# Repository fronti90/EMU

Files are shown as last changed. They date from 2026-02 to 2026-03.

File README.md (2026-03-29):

[][cc-by-nc-sa]

# EMU – Expandable Multi-material Unit
### A new take on a MMU by <a href="https://github.com/DW-Tas">DW-Tas</a> and <a href="https://github.com/igiannakas">igiannakas</a><br/>
<a href="https://ko-fi.com/O5O5OCC0K"> Ko-Fi</a>

Join me on Discord (https://discord.gg/hG2NRazKG3)   HappyHare Discord: https://discord.gg/Yt8Fe7FkNc

**Introducing the EMU, the Expandable Multi-material Unit from down under.** The EMU is a modular, flexible, upgradable, reliable and service-friendly MMU designed around the proven filamentalist V3 platform.

The EMU supports any number of lanes and base configurations; whether it is a **single lane setup** to assist filament loading, a **dual lane configuration** for endless spool, or a **multi-lane, multi base unit setup** for multi-material printing. It is also **expandable**, with no re-printing of parts required when upgrading from a 2 lane to a multiple lane setup.

> [!TIP]
> ### Crossbow Filament Cutter And A4T Toolhead
> Make the EMU part of a complete system with the [Crossbow Filament Cutter](https://github.com/DW-Tas/Crossbow-Filament-Cutter) and the [A4T Toolhead](https://github.com/Armchair-Heavy-Industries/A4T).

<p align="center">
  
</p>

### Table of Contents
- [Design Objectives & Key Features](#design-objectives)
- [Render Gallery](#render-gallery)
- [Prints Gallery](#prints-gallery)
- [Documentation](/docs)
  - [BOM, Printing, Assembly and Wiring instructions](/docs/assembly_wiring)
  - [Software Setup and Calibration](/docs/software_setup)
  - [Slicer setup and optimisation for multi color prints](/docs/software_setup/05-slicer-setup.md)
- [License](#this-work-is-licensed-under-a)

### Highlights
- **Modular & Expandable** design, able to add lanes anytime and in any configuration. No reprints when upgrading from a 2 lane setup.
- **One screw or tool-free** access and servicing, even mid-print.
- **Sealed dry boxes** able to maintain humidity in the 15% range (with silica gel) or 5–8% range (with molecular sieves) for weeks.  
- **Humidity sensors** per lane for filament environmental monitoring.
- **Reliable endless spool** with no chance of the rewound filament interfering with neighbouring rolls.
- **Off-the-shelf electronics** (EBB42 with EBB36 also fully compatible).  
- **Per-lane controls** - eject button + LEDs.

<p align="center">
  
  
</p>

## Design Objectives

### Modularity & Upgradeability  
Each lane is fully self-contained, so you can choose **exactly how many lanes you need and group them as you like**. You can also **mix and match** lanes across multiple base units, or use a stand-alone single lane for extruder loading and print assistance. 

Expanding later is also straightforward. Just print lane expanders for the base and add another dry box assembly. There is no need to reprint or replace existing parts when upgrading from a 2 lane base. 

### Ease of Servicing 
All electrical and mechanical components are either **one screw or completely tool-free and immediately accessible**, making live troubleshooting possible even during a print. 

Access to the electronics is easy - just lift the dry box off its base for full access. The stepper tensioning screw is accessible without any dissassembly allowing on the fly tuning of filament grip. Finally, removing the filamentalist, stepper and stepper assembly is possible via one screw.

### Sealed Dry Boxes  
Each spool sits in its own purpose built, **fully sealed dry box with an integrated desiccant holder**. The boxes use foam cord in areas of potential air ingress to create a tight seal, with the clear 1.5mm PETG/PC panel also offering visibility inside the dry box.

The dry boxes can maintain humidity in the 15% range (with silica gel) or 5–8% range (with molecular sieves) for weeks. Finally, as each dry box is self contained, opening one to reload filament, doesn’t disturb its neighbours, extending the effective desiccant life.

<p align="center">
  
</p>

### Integrated Humidity Sensors 
Each lane monitors its own environment, letting you know when it’s **time to refresh the desiccant**. The humidity sensors are integrated into Mainsail (and optionally in Home Assistant for historical data tracking via the mainsail HA integration).

### Endless Spool Reliability
Dual pre-stepper sensors ensure **consistent run-out detection** and reliable re-wind, as the filament is always gripped by the stepper hobbed gear assembly. 

In addition, the isolated boxes ensure that any left over, rewound, filament cannot interfere with neighbouring lanes, **preventing a jam**.

### Built on the Filamentalist
The lane assembly is based on the proven **[filamentalist V3 design with 688 bearings](https://github.com/Enraged-Rabbit-Community/ERCF_v2/tree/master/Recommended_Options/Filamentalist_Rewinder/Filamentalist_FV3_Rewinder)** with wide spool size compatibility. Built on the 74mm filamentalist stock setup, the unit fits even the slighlty wider KVP filament spools.

<p align="center">
  
  
</p>

### Integrated Filament Driving Stepper 
Each lane has its own driving stepper inside the dry box, resulting in a compact, **fully self-contained mechanical design**. In case of mechanical issue, you can swap out filamentalist assemblies with 3 screws, unplugging 2 JST plugs and unplugging the bowden tube. 

In addition, you can **swap out complete dry boxes** by unplugging two JST plugs and the bowden tube. This is helpful if you want to maintain a particularly moisture sensitive filament undisturbed when swapping it out from the EMU.

### Simple Electronics
The recommended BOM uses **readily available EBB42 boards** (with EBB36 fully compatible). MMB v2 boards can also be reused, though without humidity sensing due to I²C limitations and a slightly more intricate wiring.

In addition, **each lane has its own ventilation fan**, ensuring the stepper drivers do not overheat, even when the unit is placed on top of a hot printer. With the EBB42 and EBB36, the ventilation fans can also be speed controlled to minimize noise.

### Easy mounting
The EMU base assembly can be securely **mounted on extrusions** or using **rubber feet** directly on the printer or besides it. In either case the **electronics remain accessible** without needing to remove the unit from its mounts.

### Per-lane Controls  
Each lane includes its own eject button, status LED, and a filament colour LED that illuminates the dry box. 

## Render Gallery
<p align="center">
  
  
</p>
<p align="center">
  
  
</p>
<br/>

## Prints Gallery
<p align="center">
  1 (4)
  1 (5)
  1 (2)
  1 (3)
</p>

## Mods to main
The following mods from the community have been adopted into the main EMU release
 - Rim roller with square nuts: [martijnvanduijneveldt](https://github.com/martijnvanduijneveldt)
 - EMU Wiring Hatch Board: [kashine6](https://github.com/kashine6)

## This work is licensed under a
[Creative Commons Attribution-NonCommercial-ShareAlike 4.0 International License][cc-by-nc-sa].

[][cc-by-nc-sa]

[cc-by-nc-sa]: http://creativecommons.org/licenses/by-nc-sa/4.0/
[cc-by-nc-sa-image]: https://licensebuttons.net/l/by-nc-sa/4.0/88x31.png
[cc-by-nc-sa-shield]: https://img.shields.io/badge/License-CC%20BY--NC--SA%204.0-lightgrey.svg

## License clarification regarding non-commercial use:
The non-commercial aspect of this license is for cases where EMU is the product, not the use of EMU to create products.<br/>
I.e. If you wish to sell EMU as a product, you would need to seek a commercial license before doing so. </br>
It is NOT intended to prevent the use of EMU with a printer that you use to provide commercial services. If you want to run EMU in your print farm, go right ahead.

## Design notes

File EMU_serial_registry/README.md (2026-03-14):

# EMU – Expandable Multi-material Unit - Official Serial Registry

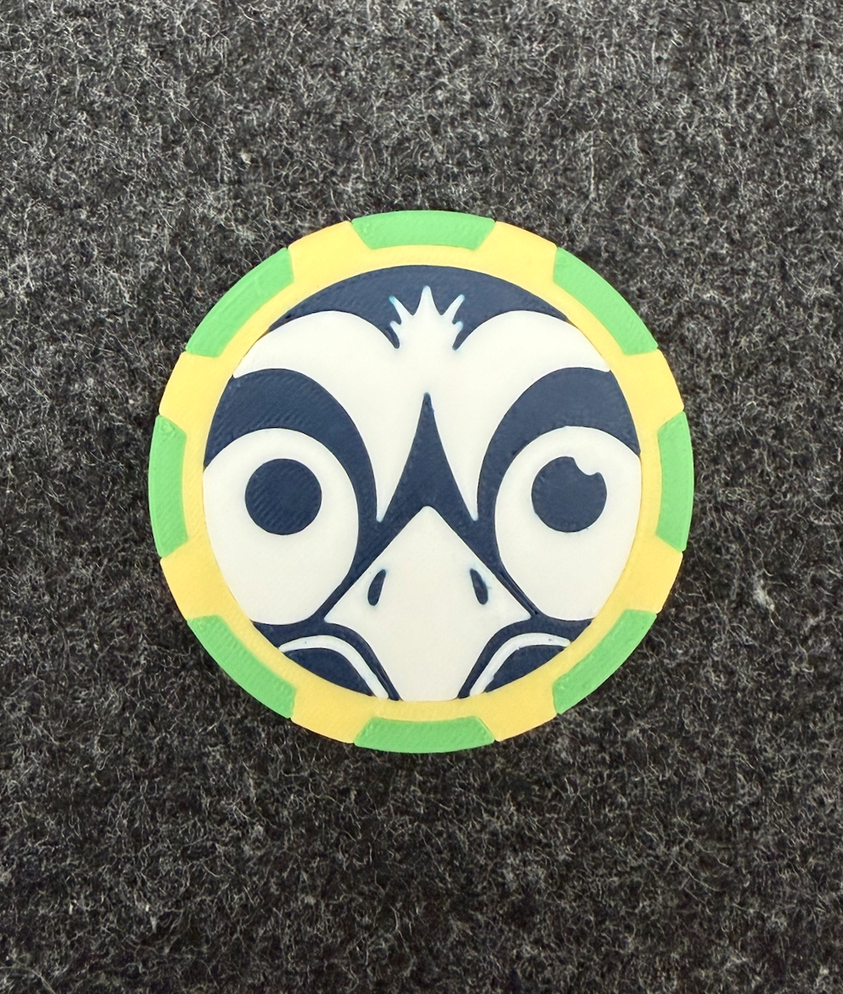
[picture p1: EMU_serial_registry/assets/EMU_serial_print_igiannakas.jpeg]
EMU Serial Print by igiannakas


**Serial #0000:** DW Tas</br>
**Serial #0001:** igiannakas</br>
**Serial #0002:** Martijn</br>
**Serial #0003:** burkfers</br>
**Serial #0004:** WilLawUK</br>
**Serial #0005:** jacksky6</br>
**Serial #0006:** Heiliger-Gral</br>
**Serial #0007:** drachenkaetzchen</br>
**Serial #0008:** fronti</br>
**Serial #0009:** pajtaz</br>
**Serial #0010:** WoodWorker</br>
**Serial #0011:** Dragi2k</br>
**Serial #0012:** TheMeanCanEHdian</br>
**Serial #0013:** Bender</br>
**Serial #0014:** Pie36</br>
**Serial #0015:** ammaze</br>
**Serial #0016:** Doak</br>
**Serial #0017:** dw.tas</br>
</br>

### How to register:
Submit your build at [dwtas.net/EMUSerial](https://dwtas.net/EMUSerial). Sign in with Discord, upload a photo of your completed EMU Maker chip and unit, and a maintainer will review your submission.

Print [at least a two color version of the EMU Maker chip](https://github.com/DW-Tas/EMU/tree/main/EMU_serial_registry/serial_print_file). If your EMU lane can reach 4+ colors, try to use them all!

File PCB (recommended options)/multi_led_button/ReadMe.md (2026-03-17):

## EMU LED PCB

The **EMU LED PCB** is a dedicated PCB designed for the EMU to enable dynamic lighting effects on the eject button assembly. It also simplifies wiring and reduces the need for soldering.

LED PCB

## BOM variations vs. baseline EMU BOM
Do not purchase the below from the base BOM:
1. 1 less neopixel
2. 1 less D2F-L switch
3. 4 less 6x3mm magnets

Add the below to the base BOM, depending on your LED PCB source:
1. 1x JST-XH 5 pin PCB header

## Manual
Assembly and wiring instructions are outlined [in the manual](https://github.com/DW-Tas/EMU/blob/main/PCB%20(recommended%20options)/multi_led_button/EMU%20LED%20Button%20PCB%20Assembly%20Manual.pdf).

## Sourcing
The hatch board PCBs can be sourced from the below location:
1. [Aliexpress](https://www.aliexpress.com/item/1005011529532141.html) in sets of 5

Alternatively use the supplied gerber, BOM and pick and place files to order from your favourite PCB manufacturer.

## Lighting effects
The multiple LEDs incorporated in the eject button allow you to create loading/unloading animations like the below. Also the integrated SMD switch provides a more tactile feel vs. the D2F switch and magnet assembly. 

The lighting effects are enabled automatically by happy hare. No separate configuration is required.

https://github.com/user-attachments/assets/2f268710-e0a5-41e1-b007-02235ff379cc

## This work is licensed under a
[Creative Commons Attribution-NonCommercial-ShareAlike 4.0 International License][cc-by-nc-sa].

[][cc-by-nc-sa]

[cc-by-nc-sa]: http://creativecommons.org/licenses/by-nc-sa/4.0/
[cc-by-nc-sa-image]: https://licensebuttons.net/l/by-nc-sa/4.0/88x31.png
[cc-by-nc-sa-shield]: https://img.shields.io/badge/License-CC%20BY--NC--SA%204.0-lightgrey.svg

## License clarification regarding non-commercial use:
The non-commercial aspect of this license is for cases where EMU is the product, not the use of EMU to create products.<br/>
I.e. If you wish to sell EMU as a product, you would need to seek a commercial license before doing so. </br>
It is NOT intended to prevent the use of EMU with a printer that you use to provide commercial services. If you want to run EMU in your print farm, go right ahead.

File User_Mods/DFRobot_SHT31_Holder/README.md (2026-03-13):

# DFRobot SHT31 Temperature & Humidity Sensor Holder

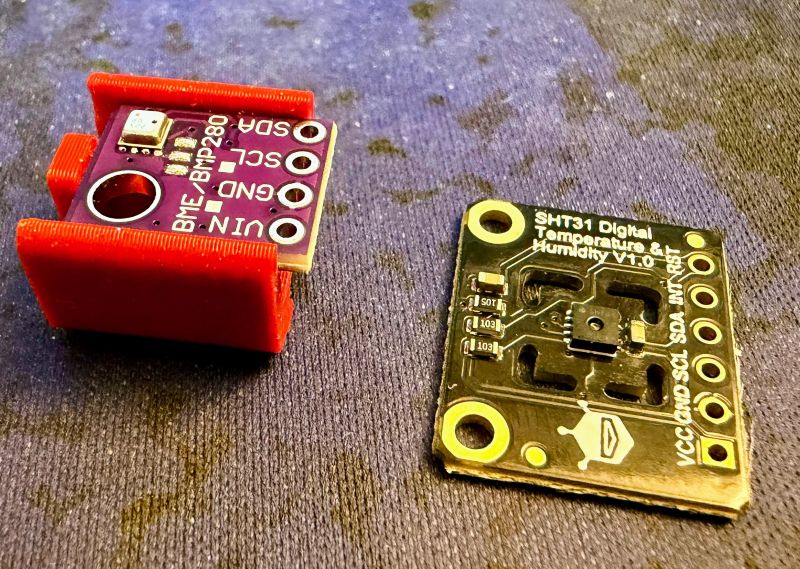
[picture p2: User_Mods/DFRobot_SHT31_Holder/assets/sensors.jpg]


## Overview
High(er) accuracy temperature & humidity sensor for use in the box instead of the standard BME280.

- Pros
    - ±2%RH at 0%RH to 100%RH (at 25°C）humidity accuracy Vs. ±3%RH 20%RH to 80%RH
    - -40°C to 125°C temperature detection range Vs. -40°C to 85°C range (although if its that hot, you've got bigger problems!)
    - Legit Fermion sensor Vs. potential BME280 clones

- Cons
    - Bigger footprint
    - More expensive (~£7 Vs. £4 per sensor)

## BOM
- DFRobot part no: SEN0331

## Where to get them?

Stick to suppliers with a known supply chain.

#### Worldwide
- [Mouser](https://www.mouser.co.uk/ProductDetail/DFRobot/SEN0331)
- [Digikey](https://www.digikey.co.uk/en/products/detail/dfrobot/SEN0331/12324931)

#### UK
- [ThePiHut](https://thepihut.com/products/fermion-sht31-digital-temperature-humidity-sensor?variant=42046092607683)
- [Farnell](https://uk.farnell.com/dfrobot/sen0331/temp-humidity-sensor-breakout/dp/4308263)

## Print settings
Standard EMU settings (999 walls) with shrinkage factor for your chosen filament.

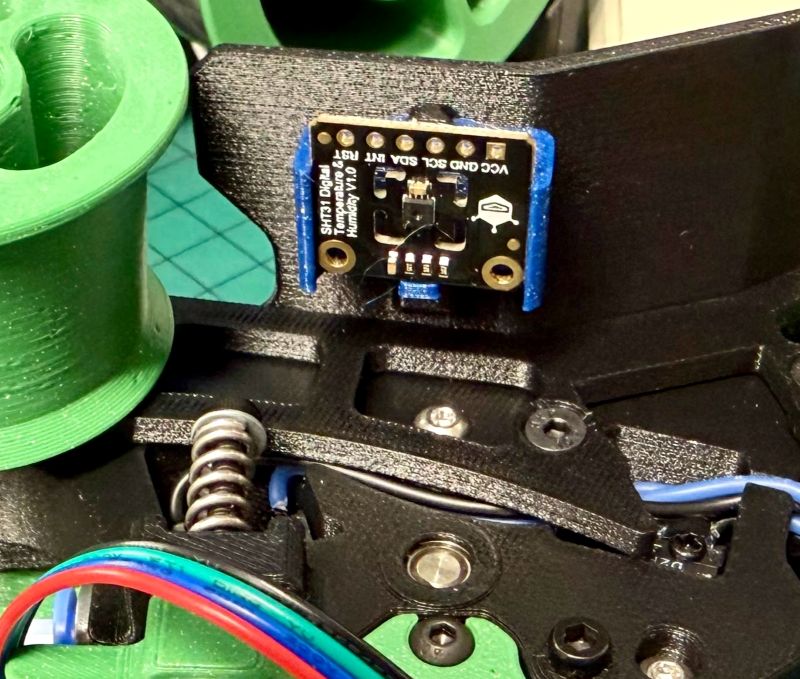
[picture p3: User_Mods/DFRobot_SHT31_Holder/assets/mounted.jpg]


## Code

By default the SHT3X klipper module expects the sensor on 68 (0x44), however the DFRobot sensors can be found at 69 (0x45) unless ADR is connected to connected to GND.

#### Example config for Lane_0 found in emu_macros.cfg

    [temperature_sensor Lane_0]
    sensor_type: SHT3X
    i2c_address: 69
    i2c_mcu: mmu0
    i2c_software_scl_pin: mmu0:PB3
    i2c_software_sda_pin: mmu0:PB4

#### How it should look when working (4 lane example)

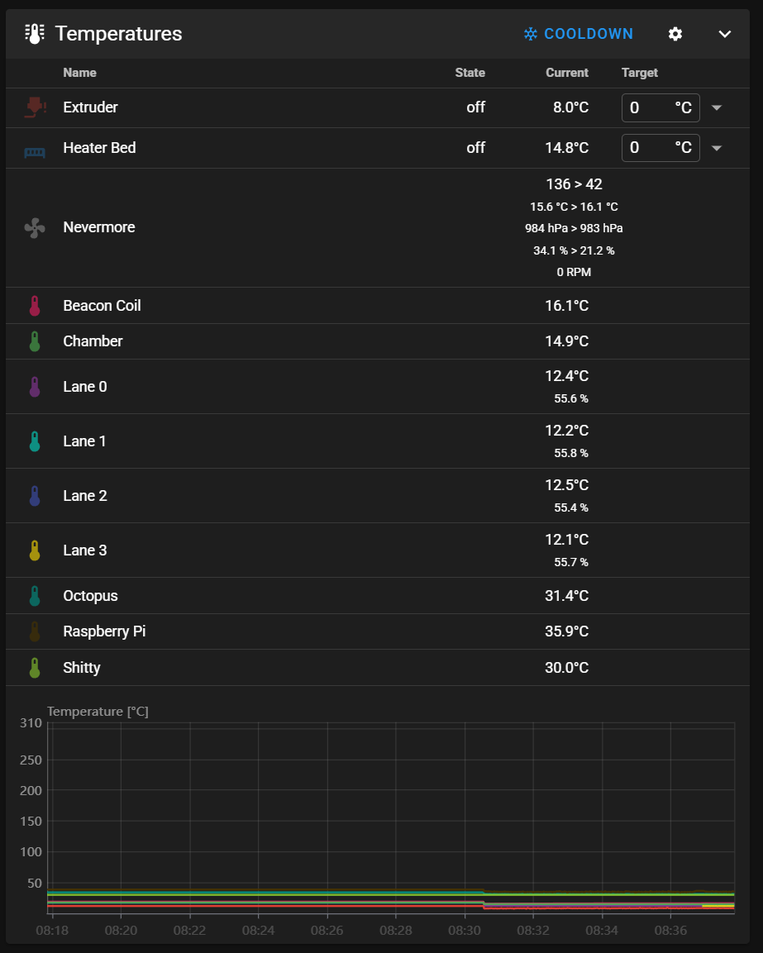
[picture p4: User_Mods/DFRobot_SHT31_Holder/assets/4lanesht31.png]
Working example


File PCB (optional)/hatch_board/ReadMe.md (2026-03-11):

## EMU Wiring Hatch Board

The **EMU Wiring Hatch Board** is a dedicated PCB designed for EMU to make wiring and assembly easier and more convenient. It replaces the printed hatch ([Box_wiring_hatch](https://github.com/DW-Tas/EMU/blob/main/STL/Box/%5Ba%5D_Box_wiring_hatch.stl)), eliminates the need to solder the Filamentalist assembly wires to the JST connectors, and removes the need to use silicone to seal gaps around the JST connector.

The EMU Wiring Hatch Board was designed and developed by <a href="https://github.com/kashine6">kashine6</a>.

## Key Features

1. **Eliminates the need to solder wires directly to JST connectors**
   - Simplifies assembly
   - Reduces soldering complexity
   - Improves maintainability, as the Filamentalist assembly can be easily unplugged from inside the base unit

2. **Simplified pre-stepper sensor connections**
   - The two pre-stepper switches no longer need to be soldered in parallel. Instead, solder the sensor and ground wires to each switch individually, then plug them into the board separately.

3. **Easier box sealing**
   - Removes the need to use silicone to seal the JST connector on the hatch cover.

4. **Wire labeling**
   - Wire labels on the PCB silkscreen reduce the chance of wiring errors during assembly.



## BOM variations vs. baseline EMU BOM
Due to the PCB being thinner than the printed box wiring hatch, **the 2x M3x8mm FHCS screws are now replaced by 2x M3x6 BHCS/SHCS screws**.

If buying pre-assembled, the corresponding straight through hole PCB header JST connectors in the BOM are no longer needed (1x JST XH 8 pin plug and 1x JST XH 4 pin plug).

If making your own, or buying bare PCBs and soldering the JST headers yourself, you'll need the below JST PCB headers:
- 3x JST XH Series Straight Through Hole PCB Header, 4 Contact
- 3x JST XH Series Straight Through Hole PCB Header, 2 Contact
- 1x JST XH Series Straight Through Hole PCB Header, 8 Contact **(part of the EMU BOM)**
- 1x JST XH Series Straight Through Hole PCB Header, 4 Contact **(part of the EMU BOM)**

## Assembly
The soldering order for the JST XH headers is important. **First, solder the 8-pin and 4-pin headers on the “outer” side (the side with the EMU logo).** Then insert and solder the headers on the inner side of the PCB.

Use a hot soldering iron (320-340C) with a medium/thin tip.

## Sourcing
The hatch board PCBs can be sourced from the below two locations:
1. [Aliexpress](https://www.aliexpress.com/item/1005011529532141.html) in sets of 5
2. [JB3D](https://jb3d.uk/product/emu-hatch-pcb/) in individual sets.

## This work is licensed under a
[Creative Commons Attribution-NonCommercial-ShareAlike 4.0 International License][cc-by-nc-sa].

[][cc-by-nc-sa]

[cc-by-nc-sa]: http://creativecommons.org/licenses/by-nc-sa/4.0/
[cc-by-nc-sa-image]: https://licensebuttons.net/l/by-nc-sa/4.0/88x31.png
[cc-by-nc-sa-shield]: https://img.shields.io/badge/License-CC%20BY--NC--SA%204.0-lightgrey.svg

## License clarification regarding non-commercial use:
The non-commercial aspect of this license is for cases where EMU is the product, not the use of EMU to create products.<br/>
I.e. If you wish to sell EMU as a product, you would need to seek a commercial license before doing so. </br>
It is NOT intended to prevent the use of EMU with a printer that you use to provide commercial services. If you want to run EMU in your print farm, go right ahead.

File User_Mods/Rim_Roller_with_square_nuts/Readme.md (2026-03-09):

# Rim roller with square nuts

A remix to use square nuts to secure the rim rollers instead of screwing directly into the plastic.

> The 1 hole version has been adopted and now resides in `STL/Filamentalist` folder.

| 1 Hole | 3 Holes |
|---|---|
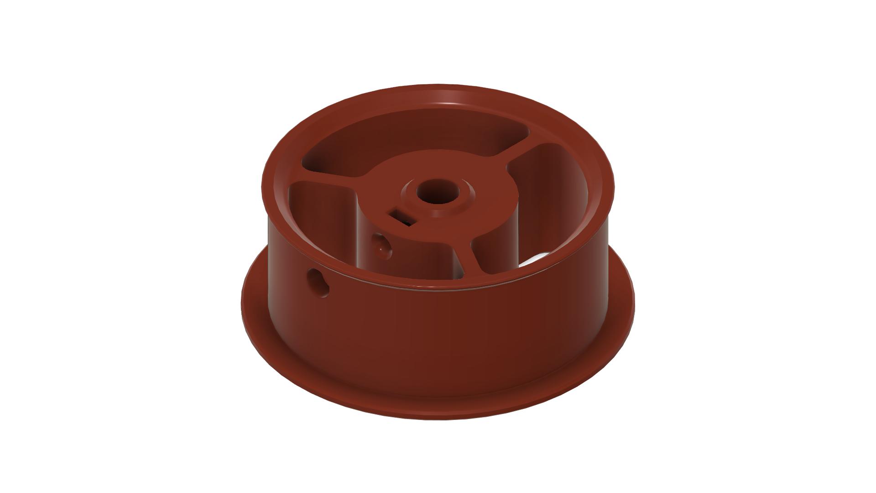
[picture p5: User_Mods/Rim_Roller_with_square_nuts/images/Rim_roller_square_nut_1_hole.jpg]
1 Hole variation
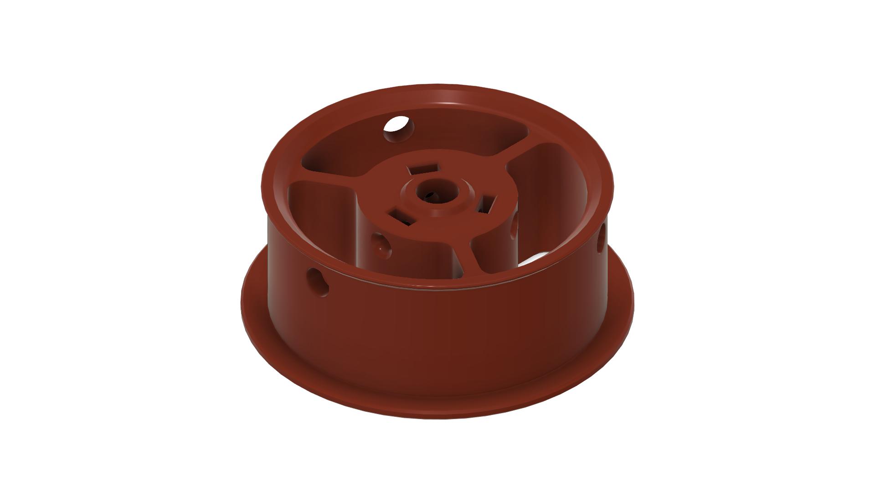
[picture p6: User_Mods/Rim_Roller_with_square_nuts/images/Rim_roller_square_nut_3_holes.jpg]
3 Holes variation
|  |  |

## Credits
- Original mod by [martijnvanduijneveldt](https://github.com/martijnvanduijneveldt)
- Improved by [DW Tas](https://github.com/DW-Tas)

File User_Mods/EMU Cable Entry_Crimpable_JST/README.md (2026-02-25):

# EMU Cable Entry with Cimpable JST sockets

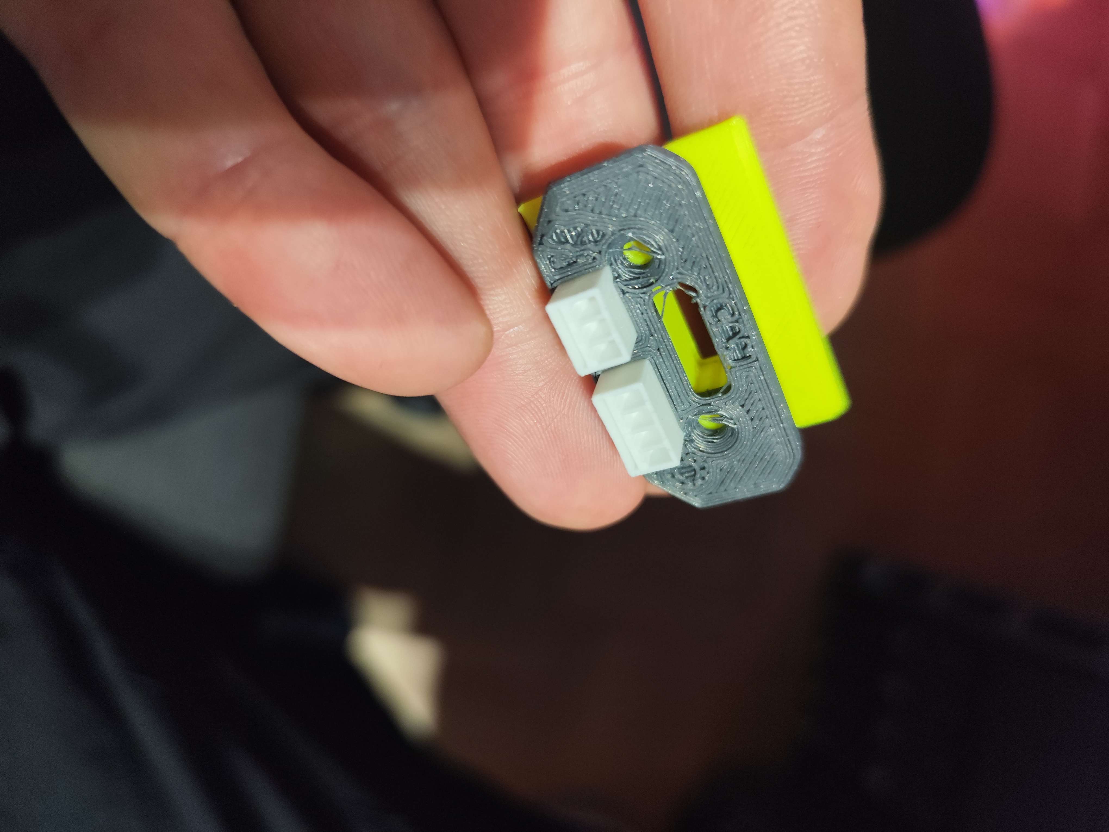
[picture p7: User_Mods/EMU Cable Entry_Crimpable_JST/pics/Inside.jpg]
Inside


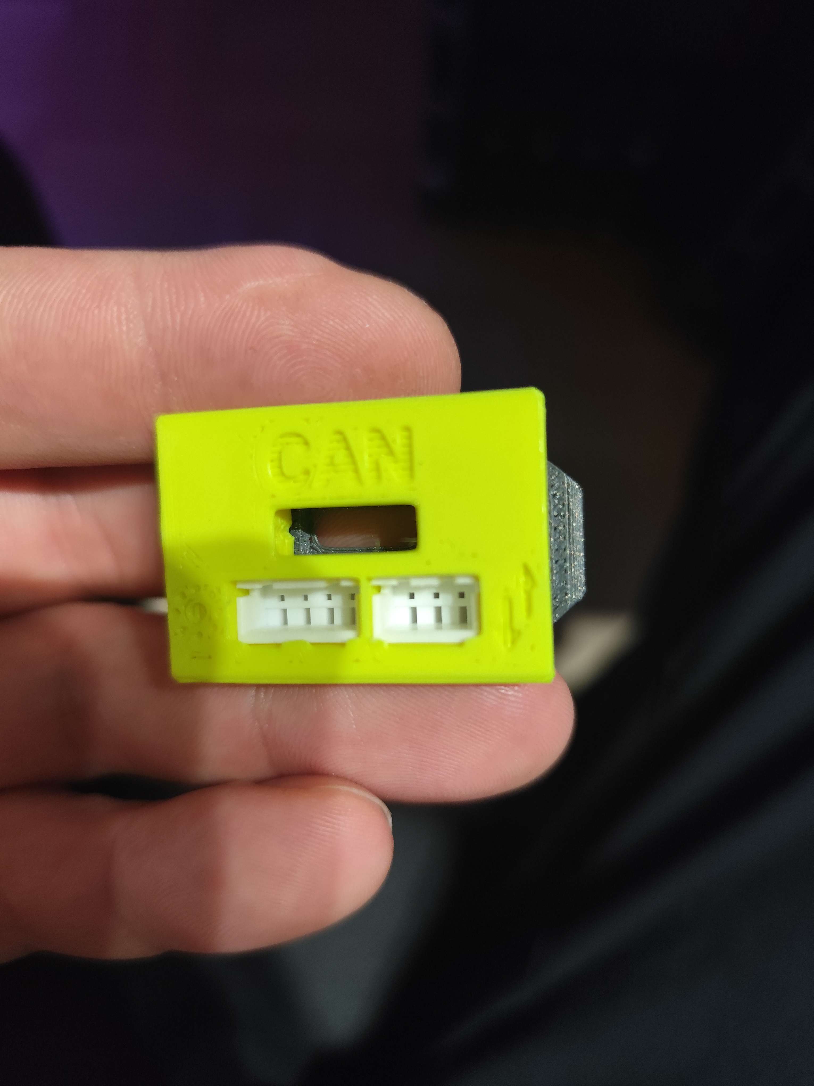
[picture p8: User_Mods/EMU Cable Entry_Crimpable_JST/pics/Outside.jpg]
Outside


for the 3 and 4 pin use these : 

https://de.aliexpress.com/item/1005008063018644.html

https://de.aliexpress.com/item/1005007287524489.html

or

https://de.aliexpress.com/item/1005009495585754.html

you need :

1x 3 pin
1x 4 pin 
per In/outled

the can bus is the origin from the BOM

by Dragi2k

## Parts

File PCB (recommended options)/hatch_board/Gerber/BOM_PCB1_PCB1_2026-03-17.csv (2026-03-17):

No. | Quantity | Comment | Designator | Footprint | Value | Manufacturer Part | Manufacturer | Supplier Part | Supplier | LCSC Part Name | Primary Category | Secondary Category
1 | 1 | PRE*2 | CN4 | CONN-TH_2P-P2.50_HX25003-2A |  | PRE*2 | HX25003-2A | C442299 | LCSC | 1x2P 间距:2.5mm 直插 系列:XH
2 | 1 | 8p | CN7 | CONN-TH_8P-P2.50-XH2.54-8P |  | 8p | Megastar(兆星) | C7429638 | LCSC | 1x8P 间距:2.5mm 直插 系列:XH
3 | 1 | SDA SCL GND 5V | I2C | CONN-TH_4P-P2.50_4PIN |  | SDA SCL GND 5V | Megastar(兆星) | C7429634 | LCSC | 1x4P 间距:2.5mm 直插 系列:XH
4 | 1 | OUT IN GND 5V | LED | CONN-TH_4P-P2.50_4PIN |  | OUT IN GND 5V | Megastar(兆星) | C7429634 | LCSC | 1x4P 间距:2.5mm 直插 系列:XH
5 | 1 | STEP | MOTOR | CONN-TH_4P-P2.50_4PIN |  | STEP | Megastar(兆星) | C7429634 | LCSC | 1x4P 间距:2.5mm 直插 系列:XH
6 | 1 | B2 B1 A1 A2 | MOTOR2 | CONN-TH_4P-P2.50_4PIN |  | B2 B1 A1 A2 | Megastar(兆星) | C7429634 | LCSC | 1x4P 间距:2.5mm 直插 系列:XH
7 | 1 | GND S | POST | CONN-TH_2P-P2.50_HX25003-2A |  | GND S | HX(Zhejiang Yueqing Hongxing Elec) | C442299 | LCSC | 1x2P 间距:2.5mm 直插 系列:XH
8 | 1 | GND S GND S | PRE*2 | CONN-TH_2P-P2.50_HX25003-2A |  | GND S GND S | HX(Zhejiang Yueqing Hongxing Elec) | C442299 | LCSC | 1x2P 间距:2.5mm 直插 系列:XH

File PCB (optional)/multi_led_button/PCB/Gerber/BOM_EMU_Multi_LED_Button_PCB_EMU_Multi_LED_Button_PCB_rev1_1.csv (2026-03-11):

No. | Quantity | Comment | Designator | Footprint | Value | Manufacturer Part | Manufacturer | Supplier Part | Supplier | LCSC Part Name | Primary Category | Secondary Category
1 | 4 | 100nF | C1,C2,C3,C4 | C0603 | 100nF | CC0603KRX7R9BB104 | YAGEO(国巨) | C14663 | LCSC | 100nF ±10% 50V | Capacitors | Multilayer Ceramic Capacitors MLCC - SMD/SMT
2 | 1 | XH2.54-5P | CN1 | CONN-TH_5P-P2.54_C9900008095 |  | XH2.54-5P |  | C9900017328 | LCSC | XH2.54-5P
3 | 4 | SK6812MINIRGBW-NW-P6 | LED1,LED2,LED3,LED4 | LED-ARRAY-SMD_6P-L3.7-W3.5-TL-RD-1 |  | SK6812MINIRGBW-NW-P6 | 欧思科光电 | C7423107 | LCSC | SK6812MINIRGBW-NW-P6 | Optoelectronics | RGB LEDs(Built-in IC)
4 | 1 | GT-TC029D-H020-L1N | SW1 | SW-SMD_L3.9-W2.9-LS4.8 |  | GT-TC029D-H020-L1N | G-Switch(品赞) | C2837082 | LCSC | 3.9*2.9*2mm 立贴 轻触开关 | Switches | Tactile Switches

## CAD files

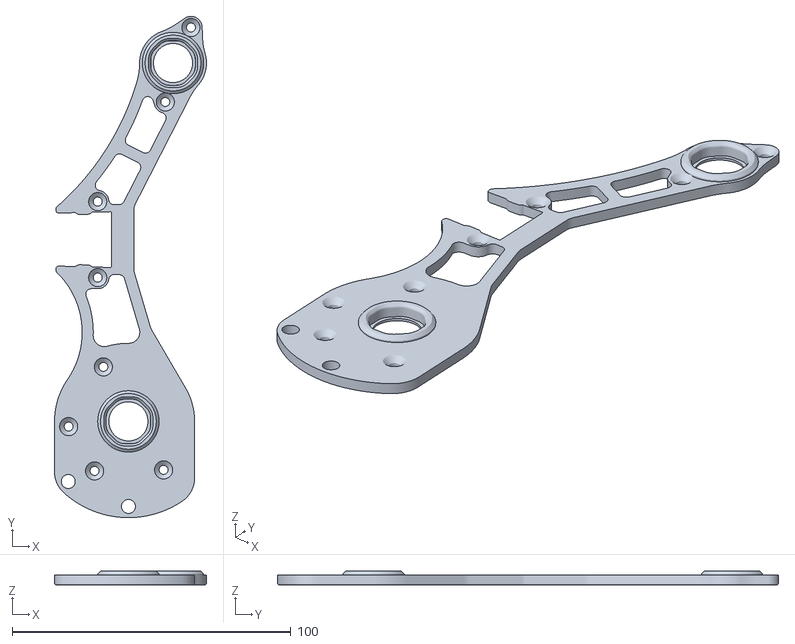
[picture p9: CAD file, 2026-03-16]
Beta parts (parts currently in testing)/Filamentalist_frame_polyhole_bearings/Chassis_L_688_Bearing_8_faces_0.05_inset.stl
54.5 x 179.7 x 5.00

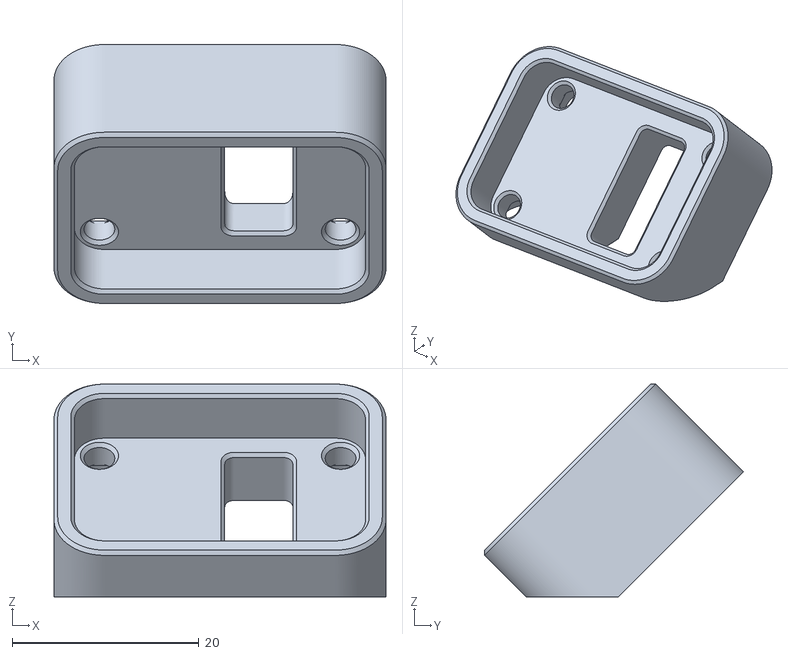
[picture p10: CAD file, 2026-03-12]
PCB (recommended options)/multi_led_button/STL/Button_Rear.stl
35.6 x 27.8 x 22.8

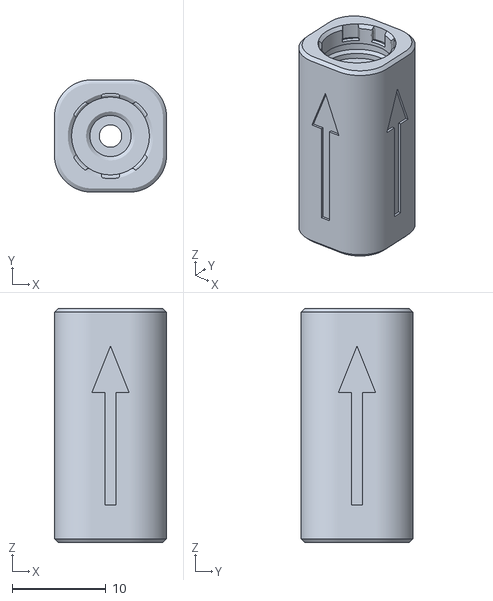
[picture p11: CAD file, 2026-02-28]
STL/Combiner/Combiner_1-1.stl
12.0 x 12.0 x 25.0

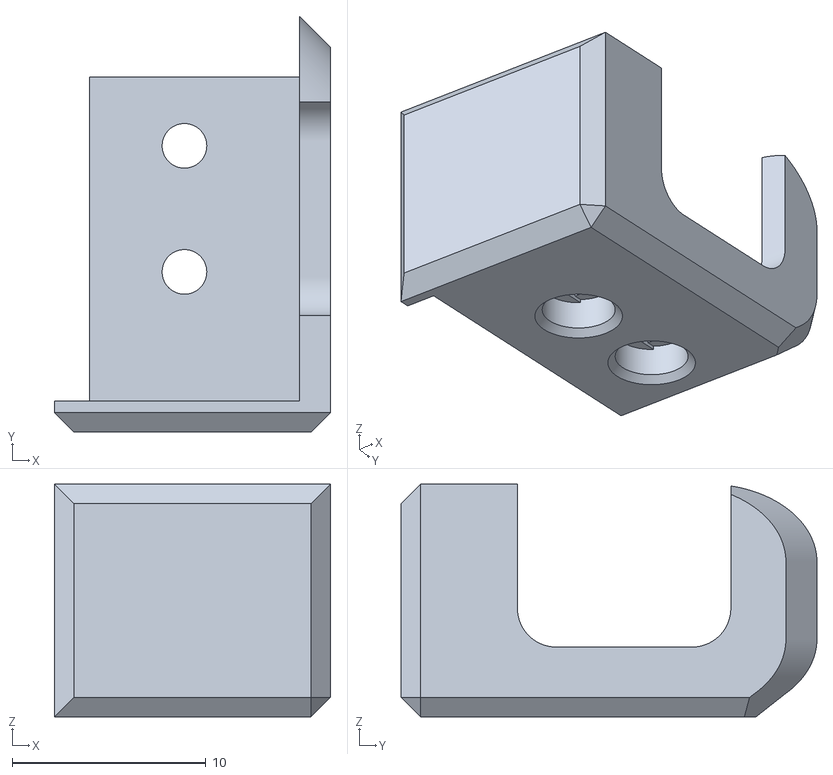
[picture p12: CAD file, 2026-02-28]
STL/Combiner/Optional/Combiners_with_sensor/[a]Combiner_sensor_cap.stl
14.2 x 21.4 x 12.0

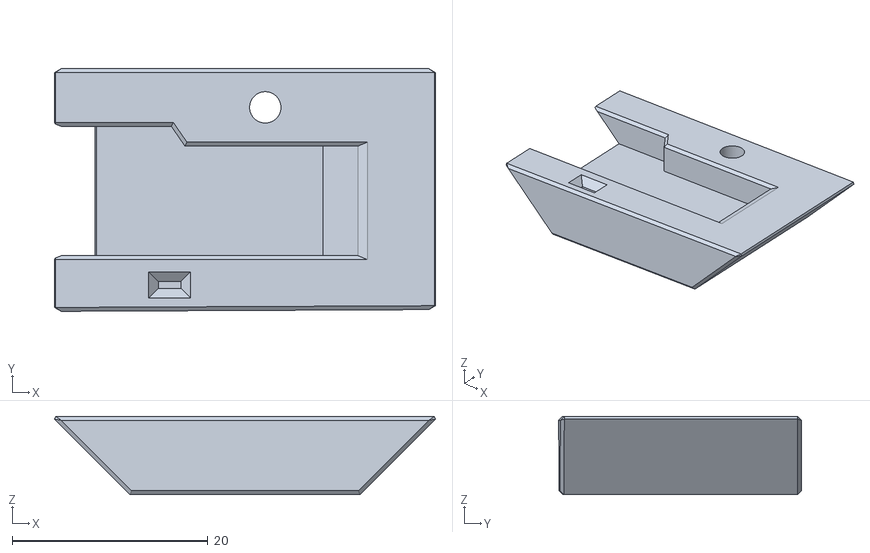
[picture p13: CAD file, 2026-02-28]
STL/Combiner/Optional/Encoder_no_sensor/[a]_Encoder_Top.stl
38.9 x 24.8 x 8.00

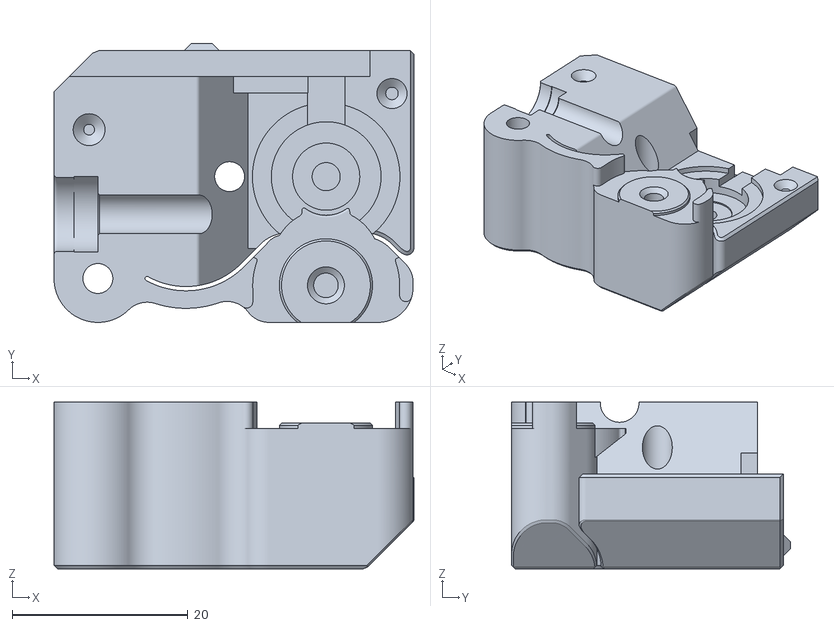
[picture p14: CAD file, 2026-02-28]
STL/Combiner/Optional/Encoder_with_sensor/Encoder_Left.stl
41.0 x 31.8 x 19.0

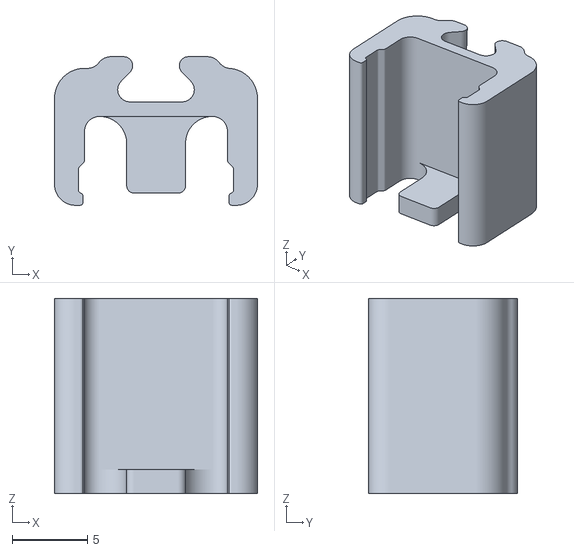
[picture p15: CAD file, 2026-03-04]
STL/Stepper/[a]_BME280_Holder.stl
13.5 x 9.88 x 13.0

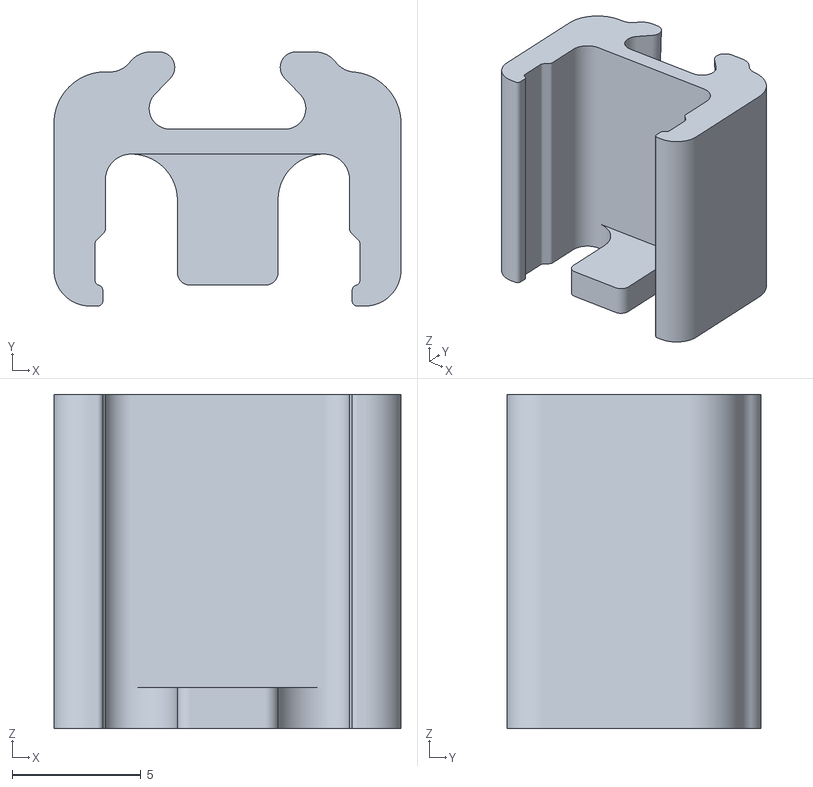
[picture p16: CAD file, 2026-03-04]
STL/Stepper/Options/[a]_BME280_Holder[+1mm].stl
13.5 x 9.88 x 13.0

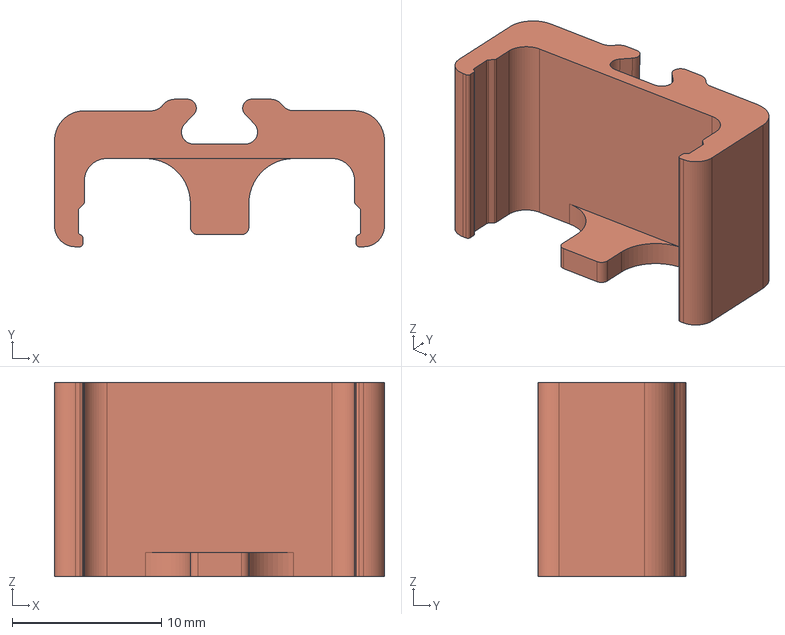
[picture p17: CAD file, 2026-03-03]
User_Mods/DFRobot_SHT31_Holder/CAD/DFRobot_SHT31_Holder.step
22.1 x 9.88 x 13.0 mm

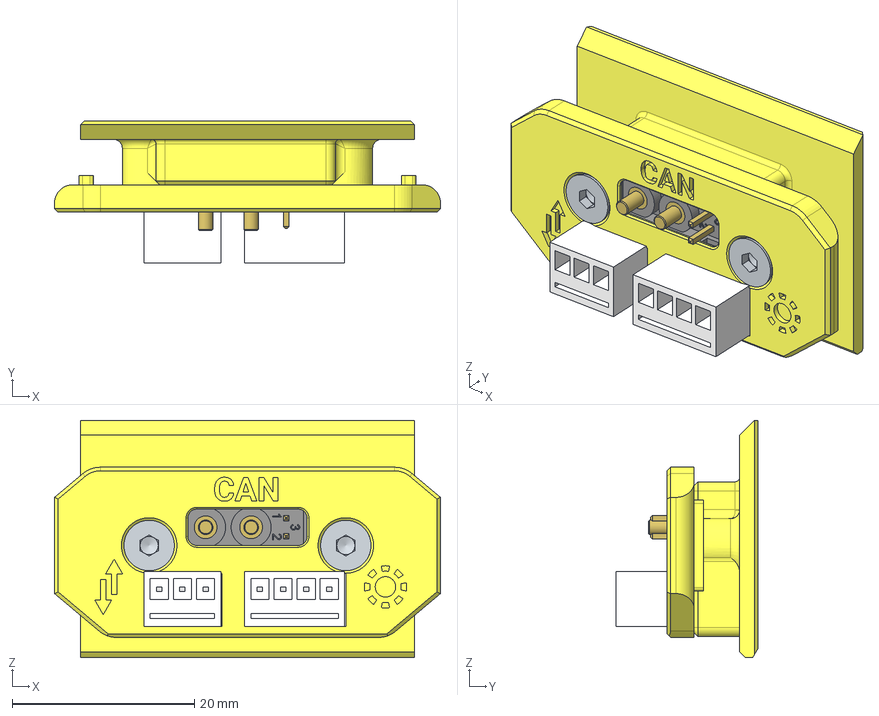
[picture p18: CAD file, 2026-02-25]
User_Mods/EMU Cable Entry_Crimpable_JST/CAD/Cable entry crimpable jst.step
42.4 x 15.6 x 26.1 mm
XT30PB
XT30PB_1
XT30PB_2
[a]_Cable_Entry-Outside_x2
Hex socket countersunk head screw M3x0.5 x 8 x 2
[a]_Cable_Entry-Inside_x2

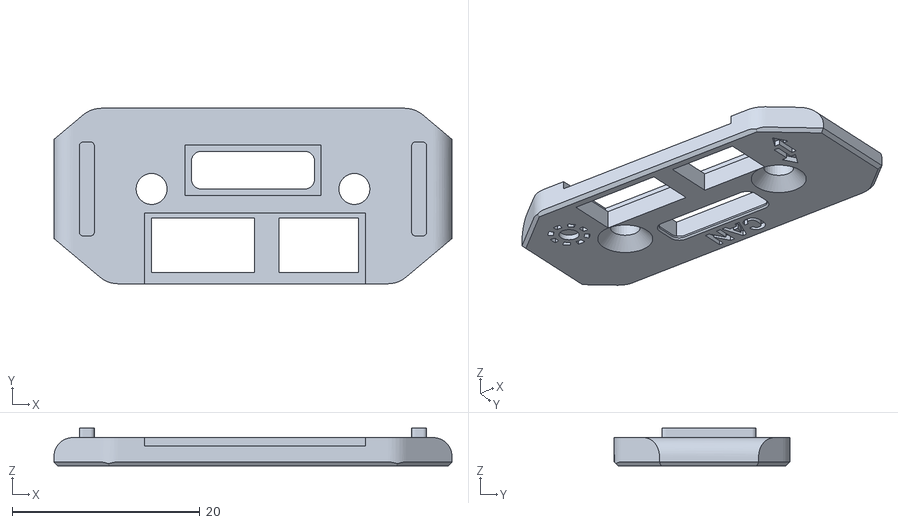
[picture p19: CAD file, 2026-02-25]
User_Mods/EMU Cable Entry_Crimpable_JST/STL/[a]_Cable_Entry-Inside_crimpable_JST.stl
42.4 x 18.7 x 4.00

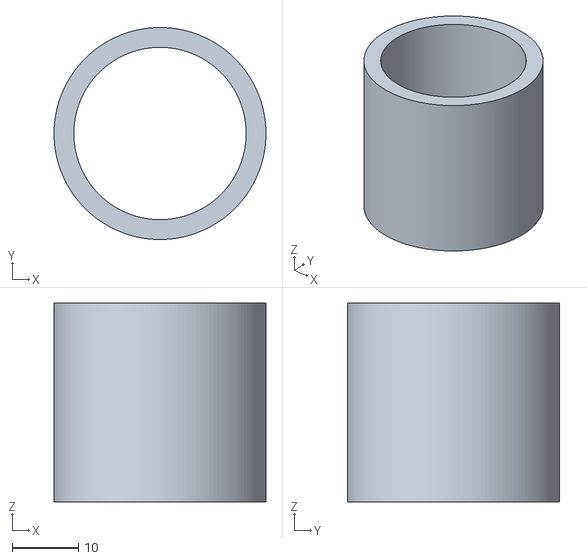
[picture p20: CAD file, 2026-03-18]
User_Mods/EMU_Roller_Rubber_Installer/STL/EMU Tube Cutter - 30mm.stl
32.0 x 32.0 x 30.0

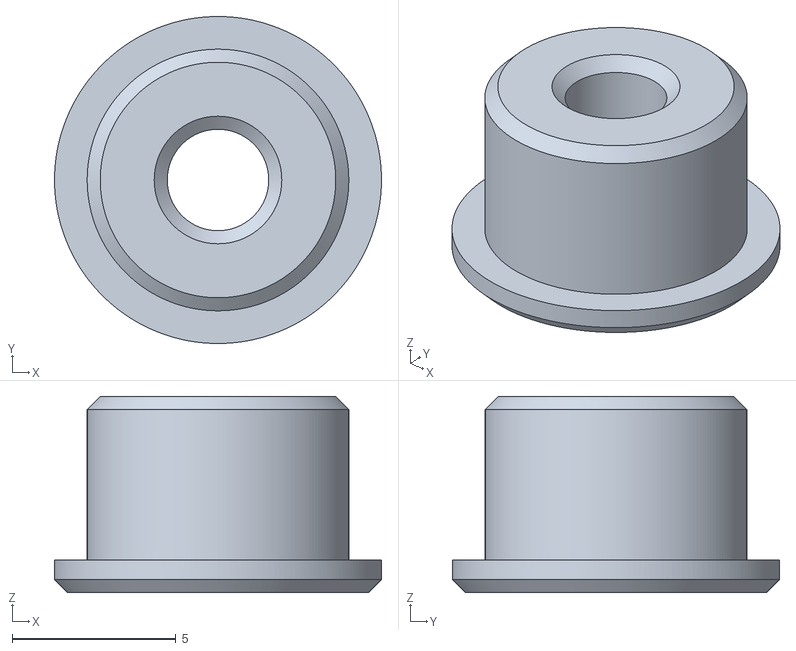
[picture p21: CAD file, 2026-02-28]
STL/Combiner/Optional/Encoder_no_sensor/688_Bushing.stl
10.0 x 10.0 x 6.00

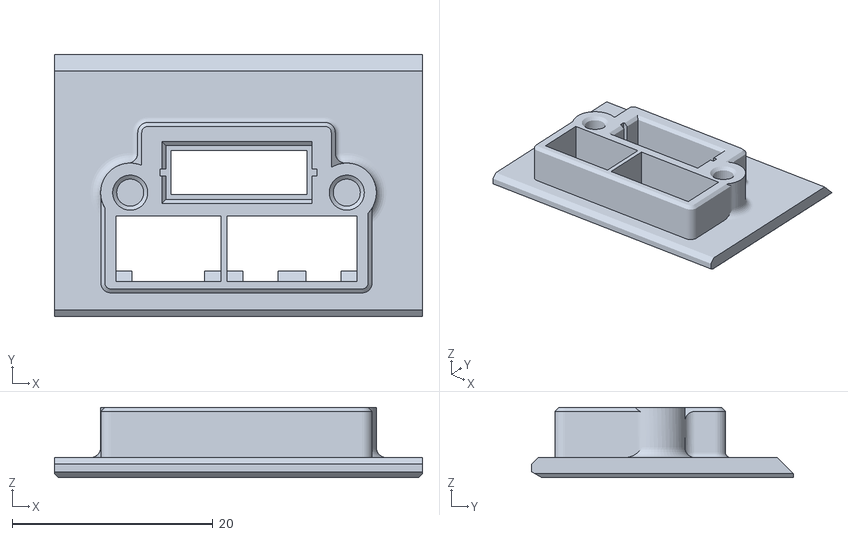
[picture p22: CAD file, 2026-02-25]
User_Mods/EMU Cable Entry_Crimpable_JST/STL/[a]_Cable_Entry-Outside_crimpable_JST.stl
36.7 x 26.1 x 7.00

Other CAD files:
Beta parts (parts currently in testing)/Filamentalist_frame_polyhole_bearings/Chassis_L_688_Bearing_8_faces_0.1_inset.stl
User_Mods/EMU_Roller_Rubber_Installer/STL/Rubber tube installer.stl
Beta parts (parts currently in testing)/Filamentalist_frame_polyhole_bearings/Chassis_L_688_Bearing_12_faces_0.05_inset.stl
Beta parts (parts currently in testing)/Filamentalist_frame_polyhole_bearings/Chassis_L_688_Bearing[polyhole].stl
Beta parts (parts currently in testing)/Filamentalist_frame_polyhole_bearings/Chassis_R_688_Bearing_12_faces_0.05_inset.stl
Beta parts (parts currently in testing)/Filamentalist_frame_polyhole_bearings/Chassis_R_688_Bearing_8_faces_0.05_inset.stl
Beta parts (parts currently in testing)/Filamentalist_frame_polyhole_bearings/Chassis_R_688_Bearing_8_faces_0.1_inset.stl
STL/Combiner/Deprecated Options/Encoder_no_sensor/12_Tooth_Encoder_Slotted_Wheel.stl
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

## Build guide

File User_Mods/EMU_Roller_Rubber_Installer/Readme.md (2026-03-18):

# Rubber Tube Cutter Guide and Installer
 
BOM:
Requires a pack of zipties - minimum 3.5mm through to 5mm wide.
 
Cutter: Slip the tube over the cutter guide and use a pair of scissors to trim both edges.
I found 30mm wide was enough for my tube but you can scale the stl to suit the coverage of the tube you receive.
 
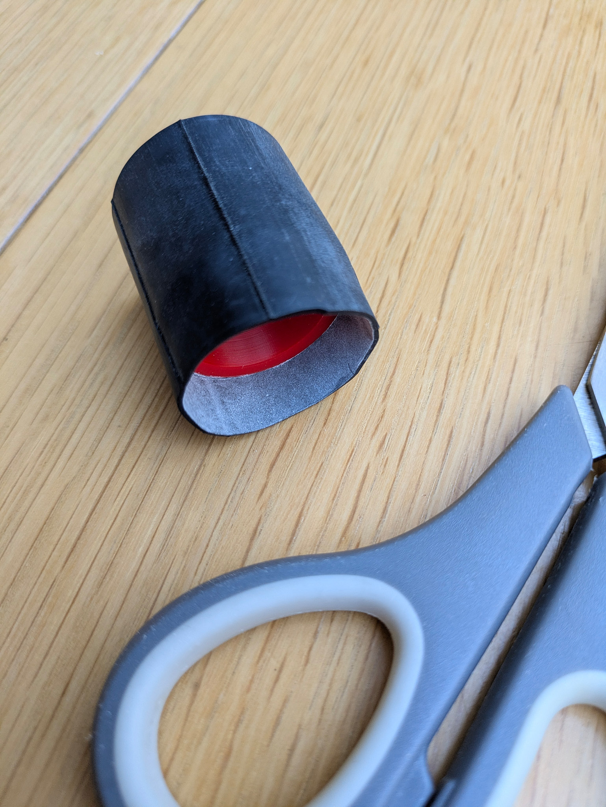
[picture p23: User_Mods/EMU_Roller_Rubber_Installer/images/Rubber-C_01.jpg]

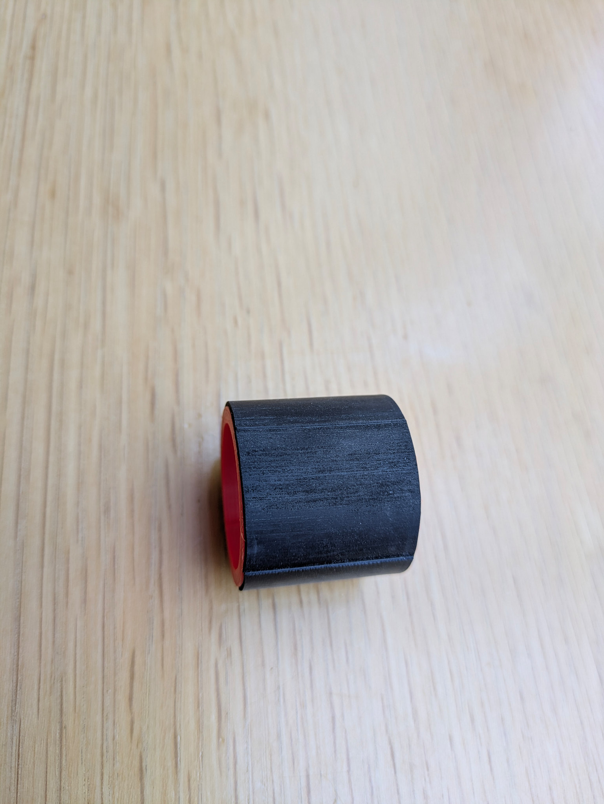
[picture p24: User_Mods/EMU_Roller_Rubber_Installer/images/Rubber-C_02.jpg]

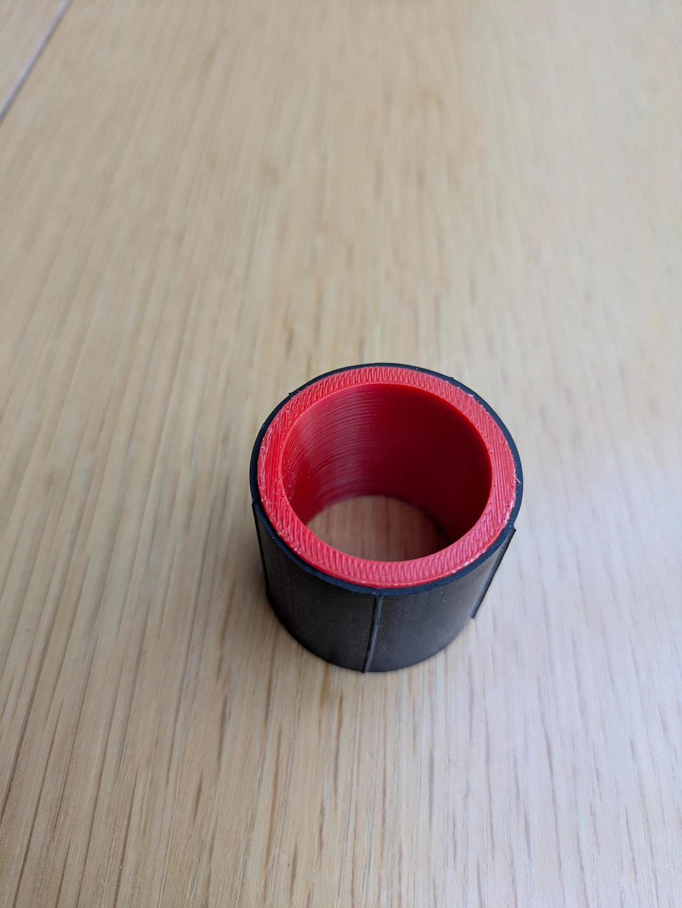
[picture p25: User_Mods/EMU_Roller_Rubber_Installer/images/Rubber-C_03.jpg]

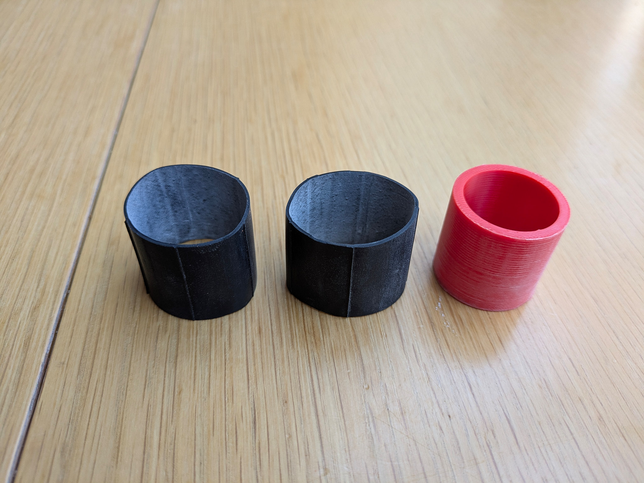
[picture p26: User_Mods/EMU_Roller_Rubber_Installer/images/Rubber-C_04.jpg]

 
Tube installer: After installing one set and fighting with the tube I created a quicker way to get the tube on the rum without skinning your knuckles. If you are good with a sharp object you can reuse the zipties across a couple of tubes by releasing them. I could get 4 rims done off a set of 4 on average. If you want to get it done quickly simply snip the cable ties once the rubber is on the rim.
 
Install the first two zipties - notice the orientation of the ziptie to assist with stretching.
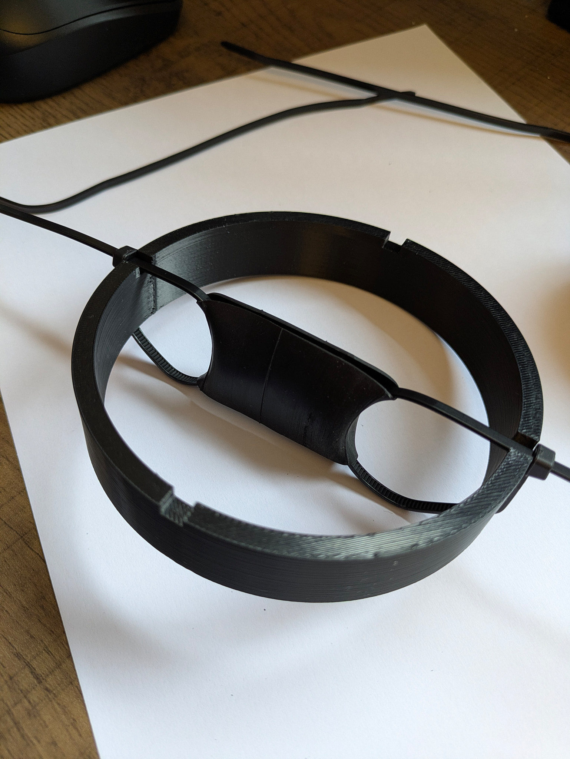
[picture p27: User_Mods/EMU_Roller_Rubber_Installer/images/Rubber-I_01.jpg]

 
Add the next two zipties
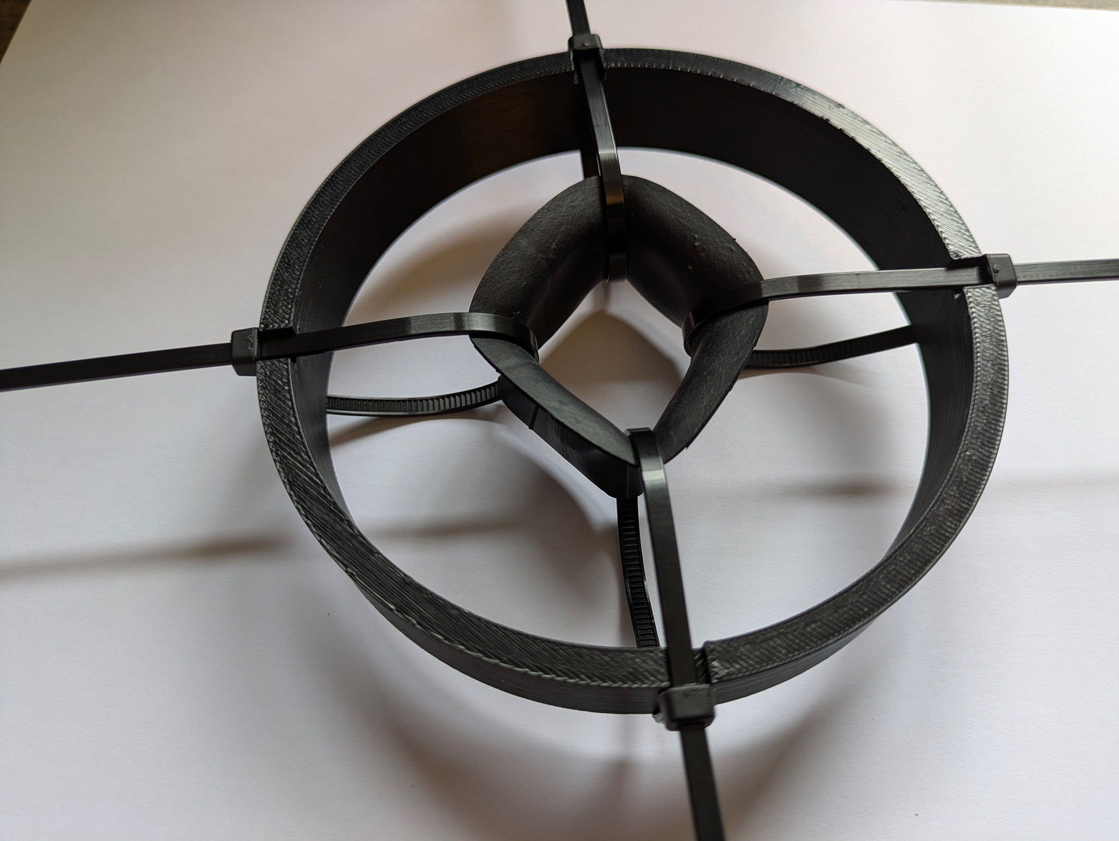
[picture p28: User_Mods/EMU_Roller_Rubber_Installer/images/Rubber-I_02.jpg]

 
Slowly stretch to size - use the roller as a guide if you need to. You can get away with slightly smaller then the rim and simply push it over the edge.
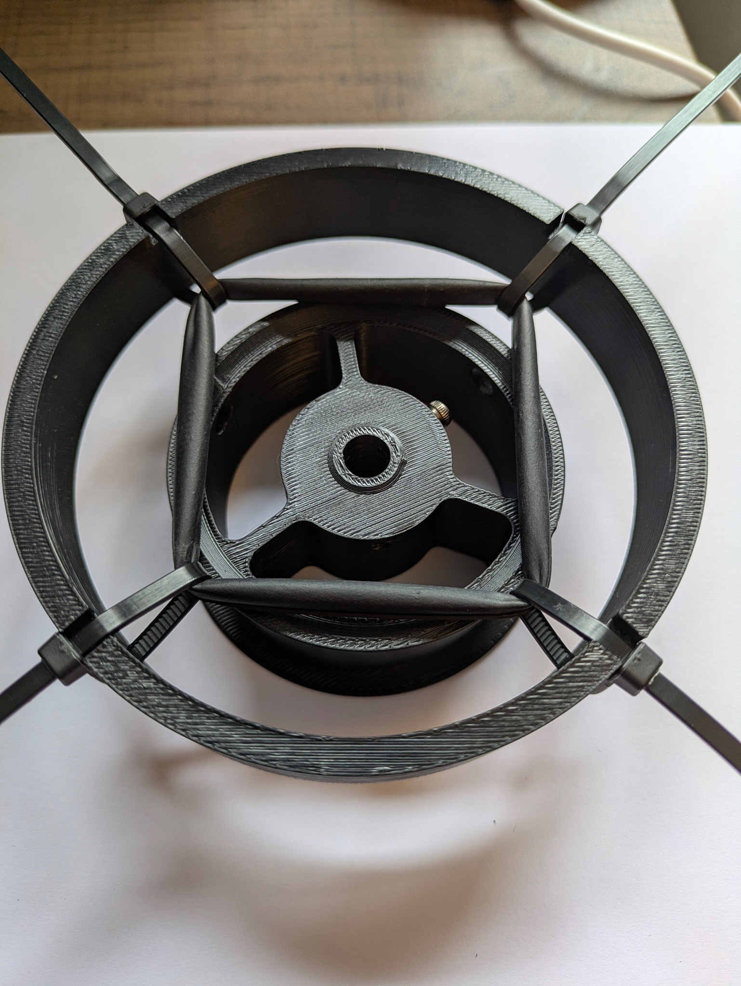
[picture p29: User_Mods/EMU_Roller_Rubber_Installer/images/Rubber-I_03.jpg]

 
Slip it on the roller
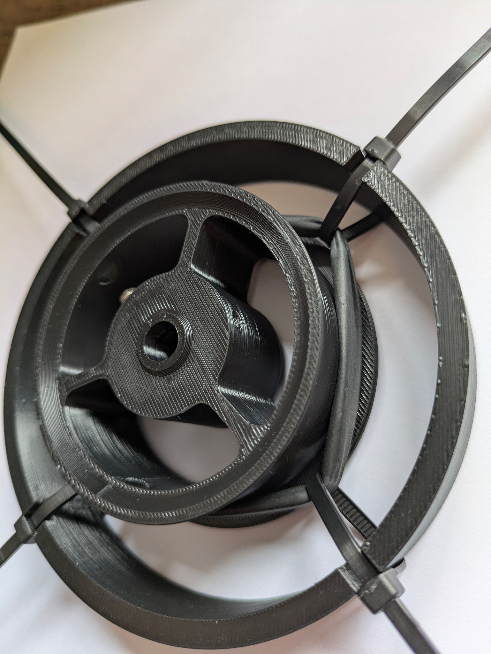
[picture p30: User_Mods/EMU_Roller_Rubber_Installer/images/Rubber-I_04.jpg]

 
Either use a sharp object (carefully) to unlock the ziptie and undo or use a pair of snips and cut them
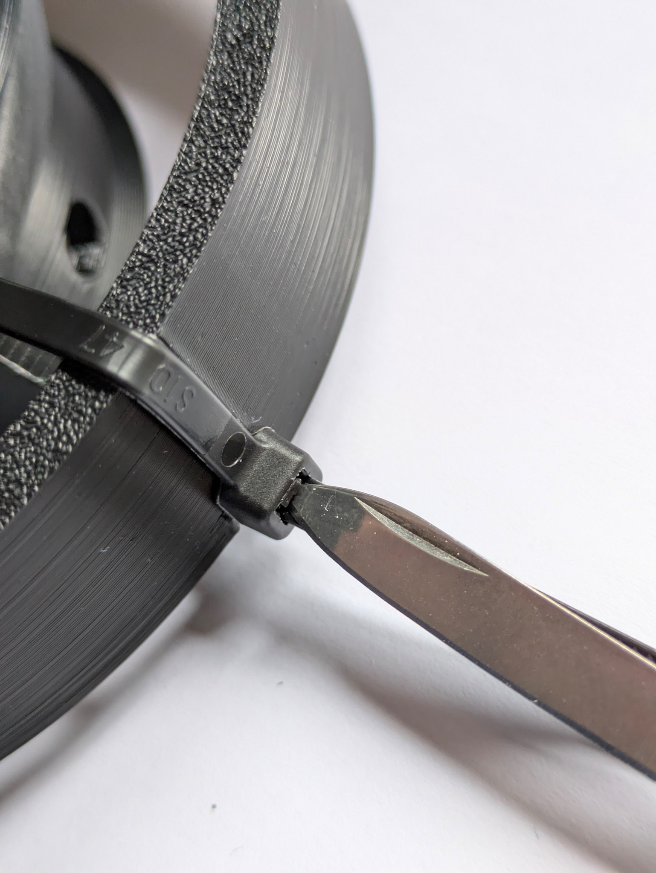
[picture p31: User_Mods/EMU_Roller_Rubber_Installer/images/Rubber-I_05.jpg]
5:

 
Slowly pull the zipies from under the tube. Careful not to split/cut the tube at this stage
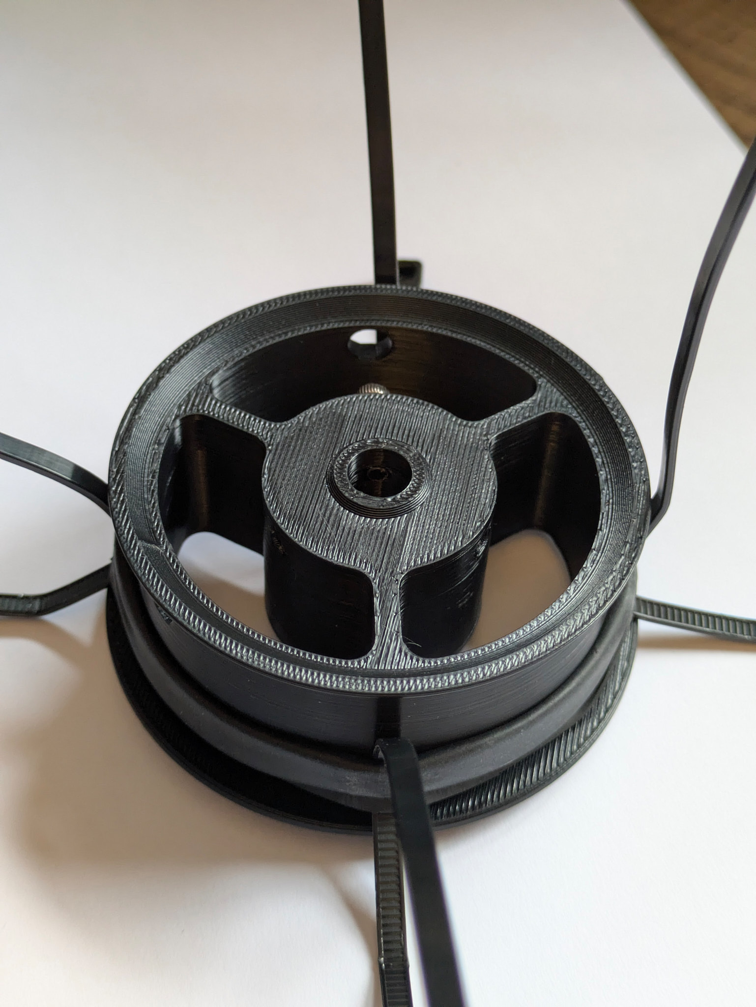
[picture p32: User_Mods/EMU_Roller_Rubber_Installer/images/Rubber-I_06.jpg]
6:

 
Rolled rubber on the roller.
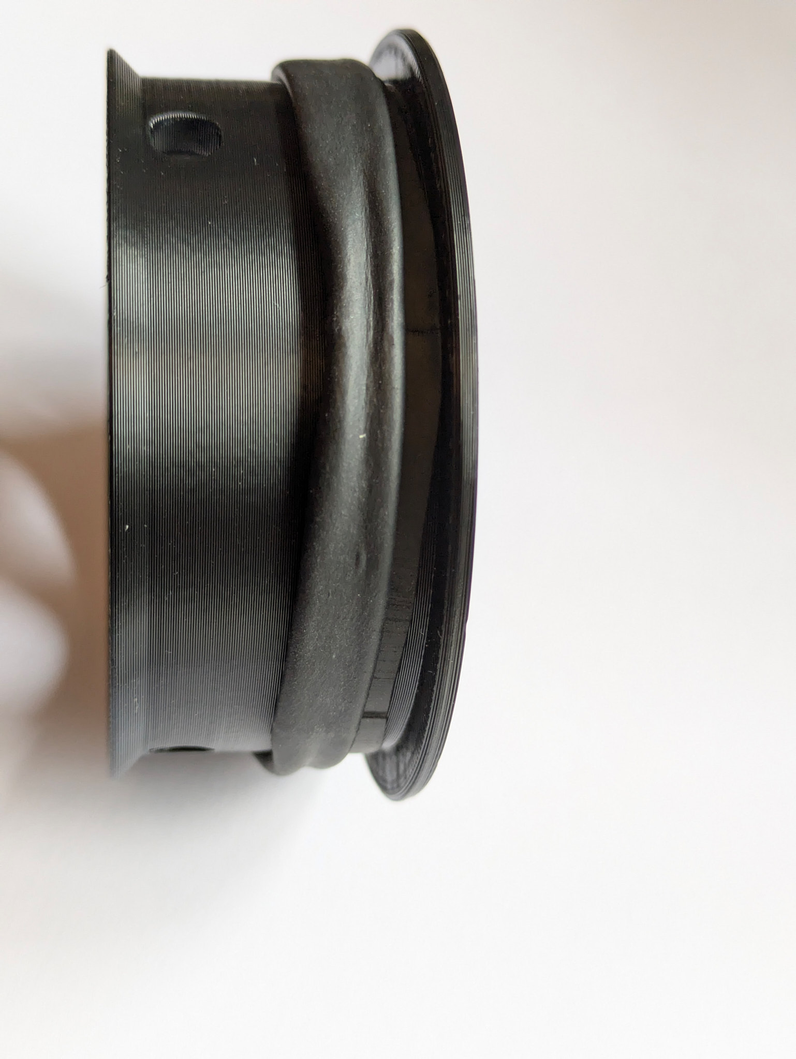
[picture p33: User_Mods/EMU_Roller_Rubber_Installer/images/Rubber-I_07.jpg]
7:

 
Unroll the rubber and shift around to cover the roller.
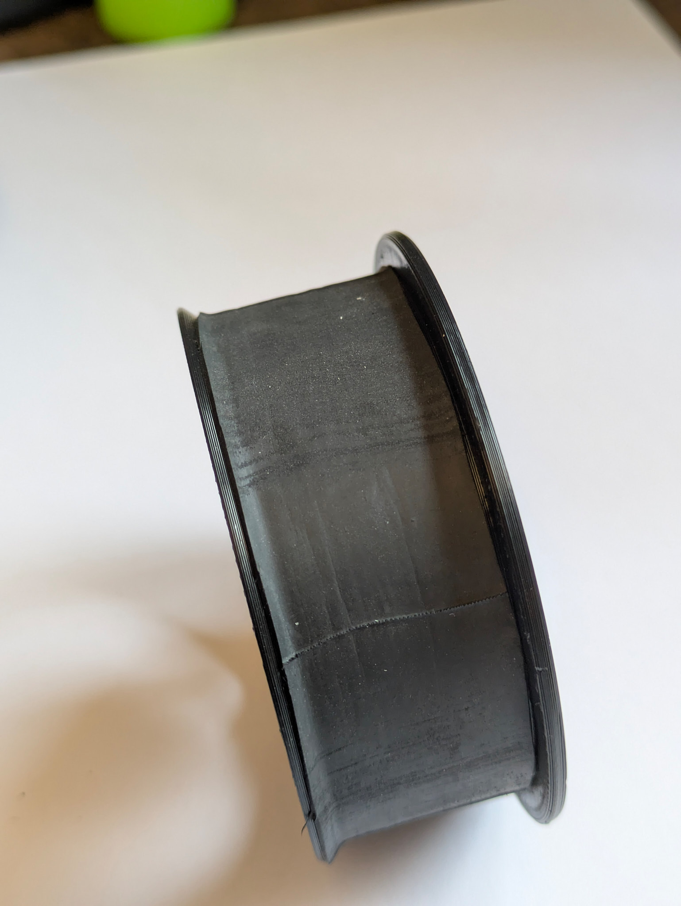
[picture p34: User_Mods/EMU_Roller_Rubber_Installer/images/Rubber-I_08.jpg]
8:


All done - now assemble onto your EMU!

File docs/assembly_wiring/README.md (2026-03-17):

# EMU - BOM, Printing, Assembly and Wiring Guide

## Table of Contents
- [EMU - BOM, Printing, Assembly and Wiring Guide](#emu---bom-printing-assembly-and-wiring-guide)
  - [Table of Contents](#table-of-contents)
  - [BOM](#bom)
  - [Recommended Upgrades](#recommended-upgrades)
  - [Print Settings](#print-settings)
    - [Filamentalist components and Lane stepper components:](#filamentalist-components-and-lane-stepper-components)
    - [Dry Box components:](#dry-box-components)
    - [Base unit components:](#base-unit-components)
  - [Assembly Videos](#assembly-videos)
    - [Part 1: Filamentalist and Stepper Assembly Guide](#part-1-filamentalist-and-stepper-assembly-guide)
    - [Part 2: Drybox Assembly Guide](#part-2-drybox-assembly-guide)
    - [Part 3: Base Assembly Guide](#part-3-base-assembly-guide)
    - [Part 4: Electronics Assembly Guide](#part-4-electronics-assembly-guide)
    - [Part 5: EMU Sync Assembly images](#part-5-emu-sync-assembly-images)
    - [Combiner:](#combiner)
  - [Wiring Instructions and Diagrams](#wiring-instructions-and-diagrams)
  - [Wiring key dimensions](#wiring-key-dimensions)
    - [Base wiring dimensions](#base-wiring-dimensions)
    - [PCB Hatch wiring dimensions](#pcb-hatch-wiring-dimensions)
    - [DIY Hatch (no pcb) wiring dimensions](#diy-hatch-no-pcb-wiring-dimensions)

<p align="center">
  
</p>

## BOM  
The EMU Bill of Materials can be found here: [Draft BOM](https://docs.google.com/spreadsheets/d/1jYJXBgpc_iLDfC17fC2LTYKrSEy5ocPbGEQ_EEOGCvI)

## Recommended Upgrades
While entirely optional, the below upgrades are highly recommended. 
1. [PCB hatch boards](https://github.com/DW-Tas/EMU/tree/main/PCB%20(recommended%20options)/hatch_board) - simplifies wiring, sealing of the box and reduces soldering need.
2. [Eject button multi-LED PCB](https://github.com/DW-Tas/EMU/tree/main/PCB%20(recommended%20options)/multi_led_button) - simplifies wiring and displays animated effects when loading / unloading filament.
3. [Proportional Sync Feedback Sensor](https://www.aliexpress.com/item/1005010470743517.html) - allows for clog, tangle detection and more accurate syncronisation between the EMU and the extruder.

## Print Settings

### Filamentalist components and Lane stepper components:
The below print settings are recommended for the filamentalist and lane stepper components. These are structural parts hence require print settings optimised for strength:
- 0.2 mm layer height
- 0.2 mm first layer height
- 4 walls
- 40% infill
- 0.4mm extrusion width (line width) throughout
- Gyroid sparse infill is recommended as it tends to warp less
- Inner Outer wall ordering, to ensure overhangs and supported areas do not sag
- Arachne wall generator
- One wall top and bottom surfaces (optional but recommended - parts look nicer)
- Disable thick bridges
- Z hop enabled to avoid nozzle scraping (0.2 is sufficient)

> [!IMPORTANT]
> The [Idler_Roller_Axle](https://github.com/DW-Tas/EMU/blob/main/STL/Filamentalist/Idler_Roller_Axle.stl) and [[a]_Stepper_Tension_Arm](https://github.com/DW-Tas/EMU/blob/main/STL/Stepper/%5Ba%5D_Stepper_Tension_Arm%5BMR693zz%5D.stl) are best to be printed with **999 walls** to ensure adequate strength of the part and less chance of breakage.

> [!IMPORTANT]
> **Parts are not shrinkage compensated** - calibrate your filament shrinkage first! If the bearings are loose, you're either under extruding, or over compensating for shrinkage.<br/>
> **Disable thick bridges** in your slicer and make sure your flow rate (EM) is on point! **Over extrusion, thick bridges and insufficient cooling will cause your sensor magnets and bearings not to fit as the bridges will sag.**

**For the TPU filamentalist CDR ring:**
- 0.2 mm layer height
- 0.2 mm first layer height
- 0.4mm extrusion width (line width) throughout
- 6 walls, so that the object is printed solid
- Avoid crossing walls enabled
- Random seam. This is important to avoid an aligned seam bump
- Inner Outer wall ordering, to ensure overhangs and supported areas do not sag
- Z Hop turned off to reduce stringing
  
> [!IMPORTANT]
> Printing TPU can be a challenge - print by object and a slight negative (-0.1) extra length on retract can help reduce stringing.

### Dry Box components:
The below print settings are recommended for the dry boxes and the desiccant holder. The dry boxes need to be as air tight as possible, hence the recommended print settings below are tuned to achieve this while keeping filament use under control.
- 0.2 mm layer height
- 0.2 mm first layer height
- 3 walls
- 15% infill
- For the lid specifically, use 4 walls and 30% infill to ensure strength in the front lip.
- 0.4mm extrusion width (line width) throughout
- Gyroid sparse infill is recommended as it tends to warp less
- Inner Outer wall ordering, to ensure dry box hatch features print with minimal sagging.
- Arachne wall generator
- One wall top and bottom surfaces (optional but recommended - parts look nicer)
- Disable thick bridges
- Z hop enabled to avoid nozzle scraping (0.2 is sufficient)

> [!IMPORTANT]
> Print with **extra first layer squish, use an adhesion promoter on the bed and in a pre-heated chamber with low fan** to prevent warping and ensure better layer adhesion. Mouse ears on the box corners may be required. Slight lifting will not impact part function.<br/>
> **Do not use mouse ears on the lid** as the slicer wrongly fills in the aesthetic lines.<br/>
> **Over extrude (only) the box and lid by ~2% (0.02)** to ensure air tightness. Increase your slicer flow multiplier (EM) by 0.02.

### Base unit components:
The below print settings are recommended for the base units and their accessories. 
- 0.2 mm layer height
- 0.2 mm first layer height
- 3 walls
- 15% infill
- 0.4mm extrusion width (line width) throughout
- Gyroid sparse infill is recommended as it tends to warp less
- Inner Outer Inner wall ordering to improve visual appearance
- Arachne wall generator
- One wall top and bottom surfaces (optional but recommended - parts look nicer)
- Disable thick bridges
- Z hop enabled to avoid nozzle scraping (0.2 is sufficient)
- For the **Eject button lens, 99 walls are recommended,** to reduce possibility of infill shining through the natural ABS

> [!IMPORTANT]
> Print with **extra first layer squish, use an adhesion promoter on the bed and in a pre-heated chamber with low fan** to prevent warping. Slight lifting will not impact part function.

> [!NOTE]
> **Paint on fuzzy skin** on the outer walls of the base unit will improve appearance.<br/>
> Paint on ONLY, not full model fuzzy skin. <br/>
> 0.1 distance, 0.1 or 0.2mm depth. Displacement method (orca slicer)

## Assembly Videos

### Part 1: Filamentalist and Stepper Assembly Guide
EMU Filamentalist and Stepper Assembly Guide (https://www.youtube.com/watch?v=FNcXC9HXUmI)
<br/>
**Errata:**
1. BMG Gear insertion is not visible in the video. Do this before adding the stepper main body and screwing it on.
2. Switch sensor screws are M2x10 self taping
3. Filament path - BMG gear alignment step is not shown in the video. Insert some filament through the unit manually, loosen the BMG gear set screw and move it back and forth. Screw down the BMG gear.
4. For the BMG tensioning arm, the bushing is no longer an option. 
5. Add a washer to the stepper tensioning arm on both sides of the spring.
6. Add a washer to the filamentalist tensioning arm on both sides of the spring.
7. Stepper body screws are all M3x20
8. Front ECAS is no longer required
9. PTFE tube lengths have been updated since the video release. [Use the dedicated cutter STL](https://github.com/DW-Tas/EMU/blob/main/STL/Tools/PTFE%20Cutter%20and%20Length%20Tool.stl) to measure and cut the PTFE tubes.
10. Front wheels now use a single M3x12 FHCS screw with a square nut placed in the corresponding wheel slot.

### Part 2: Drybox Assembly Guide
EMU Dry Box Assembly Guide (https://www.youtube.com/watch?v=JZzMyOBCdSM)
<br/>

**Errata:**
1. A threaded stand off is inserted in the front lip of the lid and secured from either side with M3x40 FHCS bolts.
2. Box and wiring hatch changes - the wiring hatch now is screwed in from the outside of the unit. Push through the hole from the inside out and then screw in place.
3. Wiring hatch foam is now glued on the box itself. The foam chord channel is on the outside of the box. 
4. The BME sensor has been relocated to the LED cover.

### Part 3: Base Assembly Guide
EMU Base Assembly Guide (https://www.youtube.com/watch?v=2SmAMuXas38)
<br/>
**Errata:**
1. Base unit top clamping screws (M3x8 FHCS) now screw into heatset inserts inserted on the other side of the frame.
2. The board and wago connectors now thread into heatset inserts from the top of the unit.

### Part 4: Electronics Assembly Guide
EMU Elecrronics Assembly Guide (https://www.youtube.com/watch?v=Iang2JYkTh8)
<br/>

**Errata:**
1. Base unit top clamping screws (M3x8 FHCS) now screw into heatset inserts inserted on the other side of the frame.
2. External combiner sensor is no longer required. That wiring part can be omitted.
3. Encoder is no longer required in the default setup. That wiring part can be omitted.
4. In the video, LED wiring is performed using the legacy method where a single LED chain was being created tied to the first EBB board. Current wiring approach wires each lane's LED's to the corresponding lane EBB, effectively moving away from one chain to N chains, where N is the number of lanes in the system. This simplifies wiring greatly and contains the wiring for each lane within the lane itself.
5. CANbus entry wires (Yellow/Green) are now connected directly to the first lane EBB42/36, ommiting the WAGO connectors. Only the power wires and LED signal wire are now connected to the WAGO connectors.

### Part 5: EMU Sync Assembly images
<table>
  <tr>
    <td>Step 1</td>
    <td>Step 2</td>
    <td>Step 3</td>
  </tr>
  <tr>
    <td>Step 4</td>
    <td>Step 5</td>
    <td>Step 6</td>
  </tr>
  <tr>
    <td>Step 7</td>
    <td>Step 8</td>
    <td>Step 9</td>
  </tr>
  <tr>
    <td>Step 10</td>
    <td>Step 11</td>
    <td>Step 12</td>
  </tr>
  <tr>
    <td>Step 13</td>
    <td>Step 14</td>
    <td>Step 15</td>
  </tr>
</table>

### Combiner:
Make sure the PTFE tube is pushed all the way inside the combiner. Not just at the ecas entry!



## Wiring Instructions and Diagrams
Depending on the number of lanes assembled, the wiring will vary slightly. Below are some initial wiring key notes to get your started.<br/>

**Wiring notes**
1. Please note that the sync feedback sensor is connected to the first lane board.
2. The CAN bus umbilical from the printer feeds power and the CAN H / L wires to the WAGO connectors in the first lane. 
3. A 24V and Ground "bus" is established throughout the base unit using the two rear WAGO connectors (WAGO 3 and WAGO 4).
4. The EBB boards connect to the power bus for power and plugged in using their Molex ports.
5. The EBB boards are daisy chained to establish the CANbus network. The first lane canbus High / Low are connected to the box cable entry and power from the first lane WAGOs (wago 3 and 4).
7. The second lane canbus High / Low wires are connected to the CAN out dupont connectors on the first board itself. This creates the daisy chain.
9. The last EBB board needs the 120Ohm resistor installed.
10. Each lane's 2nd WAGO connector is used to connect the Neopixel Out wire from the eject button to the Neopixel In wire on the dry box.

**Adding a second base unit** <br/>
You can daisy chain as many base units as you desire. Simply wire the XT30+2 CAN out port next to the last lane to the power bus and CAN H / L dupont connectors on the last EBB board. The next base unit can connect using a standard CAN Bus cable to the first unit.

**EBB 42 wiring diagram**<br/>
<p align="center">
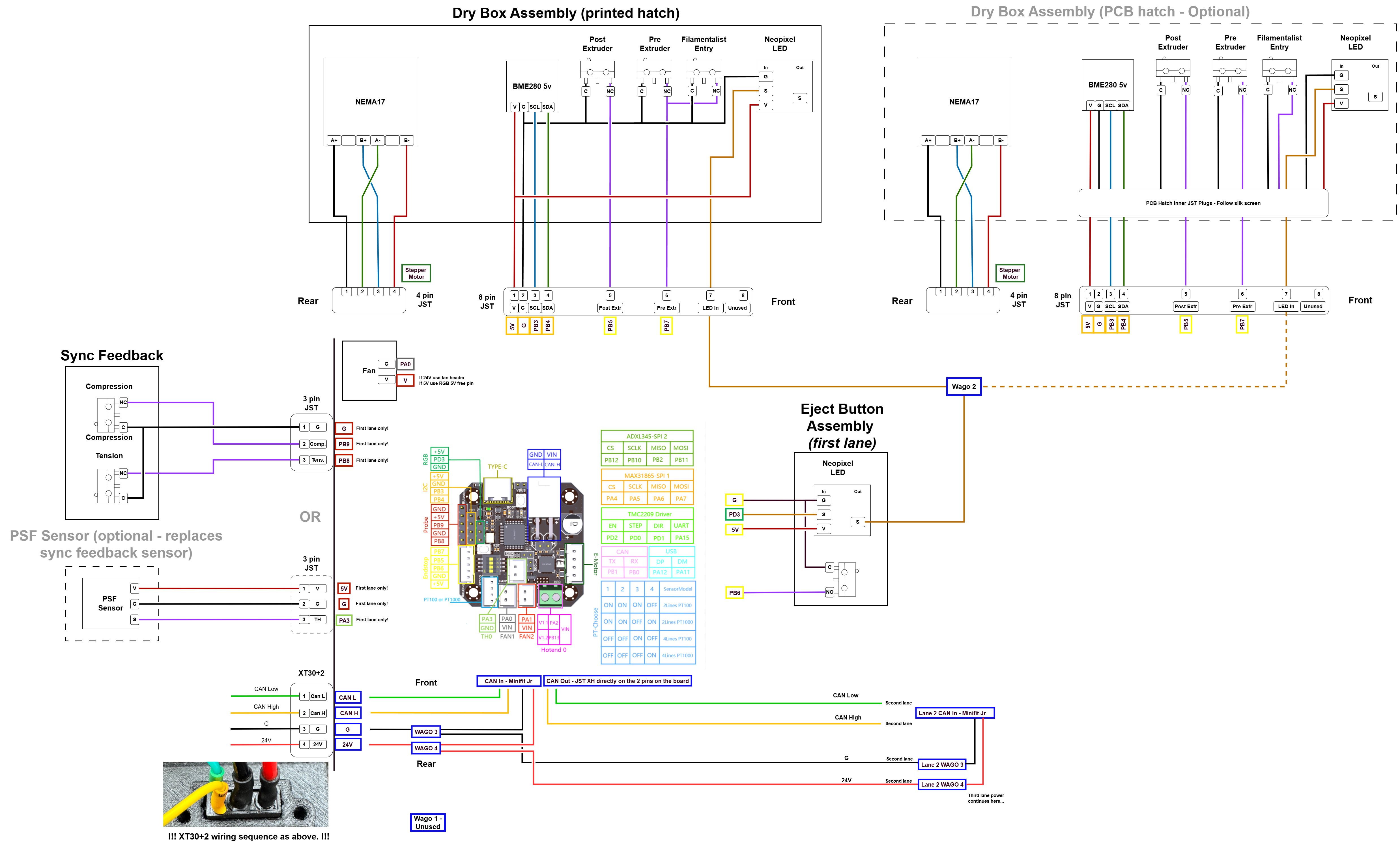
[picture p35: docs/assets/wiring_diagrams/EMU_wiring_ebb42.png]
  
</p>

**Printer PSU**<br/>
> [!WARNING]
> You need to evaluate whether your PSU has enough power headroom. This entirely depends on your printer's overall setup. Ideally **plan for ~20 Watts for an 5 lane MMU** with **each additional lane requiring approximately an additional ~2-2.5 Watts.**

Key factors to consider:
1. PSU wattage
2. How many A-B/X-Y and Z steppers 
3. At what current the main printer steppers are operating at and what print speeds you operate them at
4. Your heater cartridge wattage 
5. What other power consuming accessories are connected to the printer (cpap, heater bed if 24V etc)

Depending on the combined power consumption, you may need to consider whether a PSU upgrade is needed. 

As a rule of thumb, a 12 lane EMU build with 4 Z steppers and 2 AB steppers running moderately high currents and high print speeds on a Voron 2.4 may require a 350Watt power supply to ensure adequate power headroom.

## Wiring key dimensions

This parts describes the recommended wire length for easy assembly and maintenance.

### Base wiring dimensions

<p align="center">
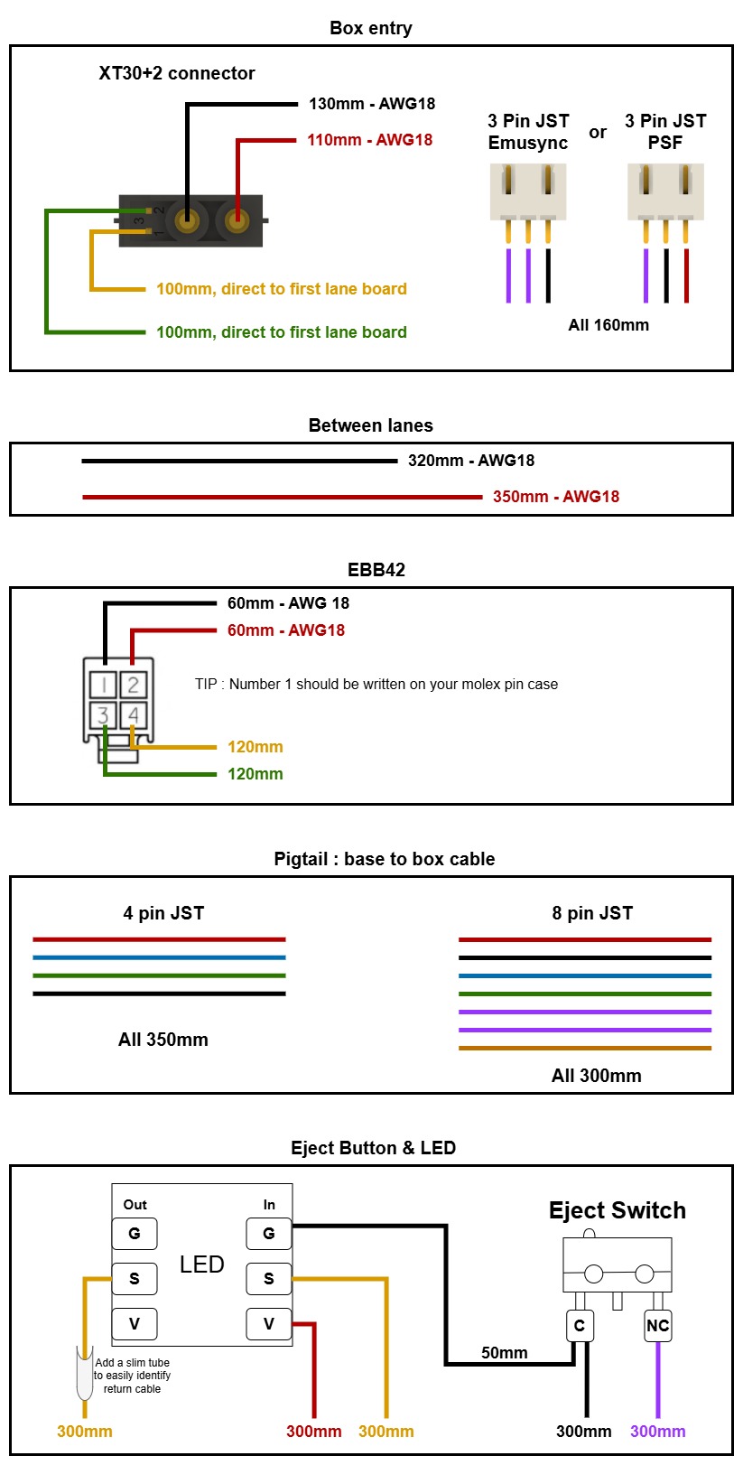
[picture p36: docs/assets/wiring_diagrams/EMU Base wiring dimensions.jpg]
  
</p>

### PCB Hatch wiring dimensions
> These dimensions are for the latest version of the PCB (Post sensor at the rear). If you have the older board (Post Sensor at the center) [refer to this image](../assets/wiring_diagrams/EMU%20PCB%20Hatch%20wiring%20dimensions%20-%20Old%20PCB.jpg) for sensor wire lengths.
<p align="center">
  
</p>

### DIY Hatch (no pcb) wiring dimensions

> These wiring dimensions assume you mount the BME sensor on the led cover and connect `5V` and `Ground` of the BME sensor to the led out `5V` and `Ground`.

<p align="center">
  
</p>

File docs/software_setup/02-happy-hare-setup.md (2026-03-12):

# Happy Hare Setup Guide

This is a provisional sofware setup guide for the EMU using Happy Hare v3. This guide is meant to be read in conjunction with the Happy Hare setup guide as found here: https://github.com/moggieuk/Happy-Hare/wiki

## Table of Contents

- [Installing Happy Hare](#installing-happy-hare)
- [Configuring the EMU hardware](#configuring-the-emu-hardware)
- [Configuring Happy Hare parameters](#configuring-happy-hare-parameters)
- [Configuring PSF and Flowguard](#configuring-psf-and-flowguard)
- [EMUSync PSF insights](#emusync-psf-insights)

## Installing Happy Hare
Install Happy Hare. More detailed instructions can be found here: https://github.com/moggieuk/Happy-Hare/wiki/Installation
```
cd ~
git clone https://github.com/moggieuk/Happy-Hare.git
cd ~/Happy-Hare
./install.sh -i
```
**Select MMU:** Pick option 16 - Other/Custom. <br/><br/>
<p align="center">
  Installer screen: Pick option 16 - Other/Custom
</p>

**Select MMU type:** Pick option 7 - Type-B (multiple filament drive steppers) with individual post-gear sensors, No Encoder <br/><br/>
<p align="center">
  Installer screen: Pick option 7 - Type-B with individual post-gear sensors, no encoder
</p>

**Select lane number:** Type the number of lanes you have set up. In my example below it is 8. <br/><br/>
<p align="center">
  Enter number of lanes (example: 8)
</p>

**Select the board used:** Pick option 15 - Not in list / Unknown <br/><br/>
<p align="center">
  Select board: option 15 Not in list / Unknown
</p>

**LED Support:** Enable LED support <br/><br/>
<p align="center">
  Enable LED support
</p>

**Endless Spool Support:** Enable Endless Spool support <br/><br/>
<p align="center">
  Enable Endless Spool support
</p>

**Include all the MMU config files:** Include all mmu config files in the printer.cfg <br/><br/>
<p align="center">
  Include MMU config files in printer.cfg
</p>

**(Optional) Mini 12864 screen support:** If you have a Mini 12864 screen, enabe the Happy Hare screen menu <br/><br/>
<p align="center">
  Enable Happy Hare menu for Mini 12864 (optional)
</p>

**Default pause/resume macros:** Include the default pause/resume macros from Happy Hare. Once the installation is complete, make sure you disable/remove any custom pause/resume macros that you may have in your existing Klipper installation! <br/><br/>
<p align="center">
  Include default pause/resume macros from Happy Hare
</p>

**EREC support:** Decline the installation of the EREC filament cutter <br/><br/>
<p align="center">
  Decline EREC filament cutter installation
</p>

**Moonraker.conf update:** Make sure your moonraker.conf contains [mmu_server] (should be inserted by HappyHare setup). Update it as per the below if it doesn't match:
```
[file_manager]
enable_object_processing: True

[mmu_server]
enable_file_preprocessor: True
enable_toolchange_next_pos: True
update_spoolman_location: True
```

<br/><br/>
Baseline setup is now complete!
<br/><br/>
## Configuring the EMU hardware

### Update your printer.cfg
Include the below items at the top of your printer.cfg. The mmu/base and client macros should already exist, following the setup wizard.
```
[include mmu/base/*.cfg]
[include mmu/addons/mmu_eject_buttons.cfg]
[include mmu/optional/client_macros.cfg]
[include emu_macros.cfg] # download this file from the EMU repo and upload to your printer
# [include mmu/addons/blobifier.cfg] # Enable this if you have a blobifier set up
```

### Update mmu/base/mmu.cfg
The Happy hare installer generates a generic mmu.cfg file that needs re-writing for the EMU. 

**Step 1: Clear the mmu.cfg file.** <br/><br/>
Start by completely deleting the content of that file and hitting save.

**Step 2: Update mmu.cfg with the EMU mcu boards definitions** <br/><br/>
For each lane you will need one distinct mcu mmu block defining the board name and the canbus UUID as noted earlier. In the example below I am using an 8 lane configuration. For a two lane setup, for example, you'd use `[mcu mmu0]` and `[mcu mmu1]` only.
```
[mcu mmu0]
canbus_uuid: your uuid 
canbus_interface: can0 # if you have multiple canbus buses, define here which canbus has the EMU units on it.

[mcu mmu1]
canbus_uuid: your uuid  
canbus_interface: can0

[mcu mmu2]
canbus_uuid: your uuid  
canbus_interface: can0

[mcu mmu3]
canbus_uuid: your uuid  
canbus_interface: can0

[mcu mmu4]
canbus_uuid: your uuid 
canbus_interface: can0

[mcu mmu5]
canbus_uuid: your uuid 
canbus_interface: can0

[mcu mmu6]
canbus_uuid: your uuid 
canbus_interface: can0

[mcu mmu7]
canbus_uuid: your uuid  
canbus_interface: can0
```

**Step 3: Update mmu.cfg with the EMU mcu board pin aliases** <br/><br/>
After the board definitions, insert the board pin aliases. 

> [!IMPORTANT]
> **Important note:** The first board defines the aliases for the tension and compression sensor too, so it is different to the rest. In the example below I am using an 8 lane configuration. Remove the corresponding `mmuN` reference from the mcu line to match the number of lanes you have (eg. `mcu: mmu0, mmu1` for a two lane setup).
```
[board_pins mmu]
mcu: mmu0, mmu1, mmu2, mmu3, mmu4, mmu5, mmu6, mmu7
aliases:
    MMU_GEAR_UART=PA15,
    MMU_GEAR_STEP=PD0,
    MMU_GEAR_DIR=PD1,
    MMU_GEAR_ENABLE=PD2,
    MMU_GEAR_DIAG=,

    MMU_NEOPIXEL=PD3,
    MMU_NEOPIXEL_LOGO=,

    MMU_PRE_GATE=PB7,
    MMU_POST_GEAR=PB5,

    MMU_TENSION=PB8,
    MMU_COMPRESSION=PB9,

    MMU_TH=PA3,

    MMU_FAN=PA0,

    EJECT_BUTTON=PB6,
```
This file is now complete! 

### Update mmu/base/mmu_hardware.cfg

**Step 1: Clear the mmu_hardware.cfg file.** <br/><br/>
Start by completely deleting the content of that file and hitting save.

**Step 2: Paste the below configuration in the mmu_hardware.cfg file**<br/><br/>
The below starter setup is for an 8 lane unit. To set up a lower lane count, paste the complete content below and change the below:
1. **num_gates: 8 -> to equal to the number of lanes you have**
2. **Delete the unecessary tmc and stepper blocks**. For example if you have a 5 lane unit, delete `[tmc2209 stepper_mmu_gear_5]`, `[tmc2209 stepper_mmu_gear_6]`, `[tmc2209 stepper_mmu_gear_7]` blocks from the below.
3. **Delete the uncesessary pre_gate_switch_pin lines and post_gear_switch_pin lines**. For example for a 5 lane setup, remove `pre_gate_switch_pin_5`, `pre_gate_switch_pin_6`, `pre_gate_switch_pin_7`, `post_gear_switch_pin_5`, `post_gear_switch_pin_6`, `post_gear_switch_pin_7`
4. **Delete the uncesessary LED blocks**: add or remove `[neopixel mmuN_leds]` to match your number of lanes
5. ***Delete the uncesessary LED effect exit leds**: Add / remove `neopixel:mmuN_leds (2)` and `neopixel:mmuN_leds (1)` from the corresponding entry and exit sections in the `[mmu_leds unit0]` block.

If you have more than 8 lanes, insert accordingly additional blocks, following the patterns illustrated in the full configuration file below.

> [!TIP]
> If during testing you see that the EMU stepper spins backwards, invert the dir_pin by adding a ! infront of it (!dir_pin).

Finally, update your toolhead sensors definition to match your setup. Here I have the extruder entry (top) sensor in my toolhead can board named EBBCan connected to pin PB6 and the toolhead sensor (post extruder) at pin PB5.
```
extruder_switch_pin: ^EBBCan: PB6
toolhead_switch_pin: ^EBBCan: PB5
```

File contents - mmu_hardware.cfg:

```
[mmu_machine]
num_gates: 8			
mmu_vendor: EMU			
mmu_version: 1.0			

selector_type: VirtualSelector
variable_bowden_lengths: 1		
variable_rotation_distances: 1		
require_bowden_move: 1		
filament_always_gripped: 1	
has_bypass: 1 

# Add your temperature and humidity sensors here for them to be visible in mainsail. One line per lane.
# Supported in HH vesion 3.42 and above.
environment_sensors:   temperature_sensor Lane_0, 
						            temperature_sensor Lane_1,
                        temperature_sensor Lane_2,
                        temperature_sensor Lane_3,
                        temperature_sensor Lane_4,
                        temperature_sensor Lane_5,
                        temperature_sensor Lane_6,
                        temperature_sensor Lane_7 

# FILAMENT DRIVE GEAR STEPPER  -----------------------------------------------------------------------------------------
[tmc2209 stepper_mmu_gear]
uart_pin: mmu0:MMU_GEAR_UART
run_current: 0.8		
hold_current: 0.2	
interpolate: False
sense_resistor: 0.110	
stealthchop_threshold: 1		

[stepper_mmu_gear]
step_pin: mmu0:MMU_GEAR_STEP
dir_pin: mmu0:MMU_GEAR_DIR
enable_pin: !mmu0:MMU_GEAR_ENABLE
rotation_distance: 22.7574		
gear_ratio: 1:1			
microsteps: 32				
full_steps_per_rotation: 200		

# Filament Drive Gear_1 --------------------------
[tmc2209 stepper_mmu_gear_1]
uart_pin: mmu1:MMU_GEAR_UART

[stepper_mmu_gear_1]
step_pin: mmu1:MMU_GEAR_STEP
dir_pin: mmu1:MMU_GEAR_DIR
enable_pin: !mmu1:MMU_GEAR_ENABLE

# Filament Drive Gear_2 --------------------------
[tmc2209 stepper_mmu_gear_2]
uart_pin: mmu2:MMU_GEAR_UART

[stepper_mmu_gear_2]
step_pin: mmu2:MMU_GEAR_STEP
dir_pin: mmu2:MMU_GEAR_DIR
enable_pin: !mmu2:MMU_GEAR_ENABLE

# Filament Drive Gear_3 --------------------------
[tmc2209 stepper_mmu_gear_3]
uart_pin: mmu3:MMU_GEAR_UART

[stepper_mmu_gear_3]
step_pin: mmu3:MMU_GEAR_STEP
dir_pin: mmu3:MMU_GEAR_DIR
enable_pin: !mmu3:MMU_GEAR_ENABLE

# Filament Drive Gear_4 --------------------------
[tmc2209 stepper_mmu_gear_4]
uart_pin: mmu4:MMU_GEAR_UART

[stepper_mmu_gear_4]
step_pin: mmu4:MMU_GEAR_STEP
dir_pin: mmu4:MMU_GEAR_DIR
enable_pin: !mmu4:MMU_GEAR_ENABLE

# Filament Drive Gear_5 --------------------------
[tmc2209 stepper_mmu_gear_5]
uart_pin: mmu5:MMU_GEAR_UART

[stepper_mmu_gear_5]
step_pin: mmu5:MMU_GEAR_STEP
dir_pin: mmu5:MMU_GEAR_DIR
enable_pin: !mmu5:MMU_GEAR_ENABLE

# Filament Drive Gear_6 --------------------------
[tmc2209 stepper_mmu_gear_6]
uart_pin: mmu6:MMU_GEAR_UART

[stepper_mmu_gear_6]
step_pin: mmu6:MMU_GEAR_STEP
dir_pin: mmu6:MMU_GEAR_DIR
enable_pin: !mmu6:MMU_GEAR_ENABLE

# Filament Drive Gear_7 --------------------------
[tmc2209 stepper_mmu_gear_7]
uart_pin: mmu7:MMU_GEAR_UART

[stepper_mmu_gear_7]
step_pin: mmu7:MMU_GEAR_STEP
dir_pin: mmu7:MMU_GEAR_DIR
enable_pin: !mmu7:MMU_GEAR_ENABLE

[mmu_sensors]
pre_gate_switch_pin_0: ^mmu0:MMU_PRE_GATE
pre_gate_switch_pin_1: ^mmu1:MMU_PRE_GATE
pre_gate_switch_pin_2: ^mmu2:MMU_PRE_GATE
pre_gate_switch_pin_3: ^mmu3:MMU_PRE_GATE
pre_gate_switch_pin_4: ^mmu4:MMU_PRE_GATE
pre_gate_switch_pin_5: ^mmu5:MMU_PRE_GATE
pre_gate_switch_pin_6: ^mmu6:MMU_PRE_GATE
pre_gate_switch_pin_7: ^mmu7:MMU_PRE_GATE

post_gear_switch_pin_0: ^mmu0:MMU_POST_GEAR
post_gear_switch_pin_1: ^mmu1:MMU_POST_GEAR
post_gear_switch_pin_2: ^mmu2:MMU_POST_GEAR
post_gear_switch_pin_3: ^mmu3:MMU_POST_GEAR
post_gear_switch_pin_4: ^mmu4:MMU_POST_GEAR
post_gear_switch_pin_5: ^mmu5:MMU_POST_GEAR
post_gear_switch_pin_6: ^mmu6:MMU_POST_GEAR
post_gear_switch_pin_7: ^mmu7:MMU_POST_GEAR

extruder_switch_pin: ^EBBCan: PB6
toolhead_switch_pin: ^EBBCan: PB5

# Section below if using the dual switch version of the EMU Sync. 
sync_feedback_tension_pin: ^mmu0:MMU_TENSION         # Compression is when you pull the bowden tubes (entry/exit) away from each other. Tension when you push the tubes together.
sync_feedback_compression_pin: ^mmu0:MMU_COMPRESSION

# Section below if using the Proportional (PSF) version of the EMU Sync. Run the calibration routine (MMU_CALIBRATE_PSENSOR) and
# update the sync_feedback_analog_max_compression, sync_feedback_analog_max_tension and sync_feedback_analog_neutral_point accordingly.
# Comment out/delete the dual switch section above and uncomment the section below to use.
#sync_feedback_analog_pin: mmu0:MMU_TH
#sync_feedback_analog_max_compression: 0.9435
#sync_feedback_analog_max_tension:     0.0982
#sync_feedback_analog_neutral_point:   0.5275

# MMU NEOPIXEL LED SUPPORT ------------------------------------------------------------------------------------

[neopixel mmu0_leds] # one block per lane (Lane 0)
pin: mmu0:MMU_NEOPIXEL
chain_count: 2			# one for the box and one for the eject button
color_order: GRBW		

[neopixel mmu1_leds] # one block per lane (Lane 1)
pin: mmu1:MMU_NEOPIXEL
chain_count: 2			
color_order: GRBW		

[neopixel mmu2_leds] # one block per lane (Lane 2)
pin: mmu2:MMU_NEOPIXEL
chain_count: 2		
color_order: GRBW	

[neopixel mmu3_leds] # one block per lane (Lane 3)
pin: mmu3:MMU_NEOPIXEL
chain_count: 2			
color_order: GRBW

[neopixel mmu4_leds] # one block per lane (Lane 4)
pin: mmu4:MMU_NEOPIXEL
chain_count: 2			
color_order: GRBW

[neopixel mmu5_leds] # one block per lane (Lane 5)
pin: mmu5:MMU_NEOPIXEL
chain_count: 2			
color_order: GRBW

[neopixel mmu6_leds] # one block per lane (Lane 6)
pin: mmu6:MMU_NEOPIXEL
chain_count: 2			
color_order: GRBW

[neopixel mmu7_leds] # one block per lane (Lane 7)
pin: mmu7:MMU_NEOPIXEL
chain_count: 2			
color_order: GRBW	

# MMU LED EFFECT SEGMENTS ----------------------------------------------------------------------------------------------
[mmu_leds unit0]
exit_leds:
  neopixel:mmu0_leds (1) # add/remove to match number of lanes
  neopixel:mmu1_leds (1)
  neopixel:mmu2_leds (1)
  neopixel:mmu3_leds (1)
  neopixel:mmu4_leds (1)
  neopixel:mmu5_leds (1)
  neopixel:mmu6_leds (1)
  neopixel:mmu7_leds (1)
entry_leds:
  neopixel:mmu0_leds (2) # add/remove to match number of lanes
  neopixel:mmu1_leds (2)
  neopixel:mmu2_leds (2)
  neopixel:mmu3_leds (2)
  neopixel:mmu4_leds (2)
  neopixel:mmu5_leds (2)
  neopixel:mmu6_leds (2)
  neopixel:mmu7_leds (2)
frame_rate: 24

enabled: True                           # LEDs are enabled at startup
animation: True                         # Use led-animation-effects
exit_effect: gate_status                # gate_status in the eject buttons
entry_effect: filament_color            # filament_color in the dry box LED
status_effect: off                      # no status LED is on the unit
logo_effect: (0, 0, 0)                  # no Logo LED is on the unit
white_light: (1, 1, 1)                  # RGB color for static white light
black_light: (1, 1, 1)                  # RGB color used to represent "black" filament
empty_light: (0.0, 0.0, 0.0)            # Empty gate has eject button "off"

effect_loading:            mmu_clockwise_fast, (0, 0, 0.4)
effect_loading_extruder:   mmu_clockwise_slow, (0, 0, 1)
effect_unloading:          mmu_anticlock_fast, (0, 0, 0.4)
effect_unloading_extruder: mmu_anticlock_slow, (0, 0, 1)
effect_heating:            mmu_breathing_red,       (0.3, 0, 0)
effect_selecting:          mmu_white_fast,          (0.2, 0.2, 0.2)
effect_checking:           mmu_white_fast,          (0.8, 0.8, 0.8)
effect_initialized:        mmu_rainbow,             (0.5, 0.2, 0)
effect_error:              mmu_strobe,              (1, 0, 0)
effect_complete:           mmu_sparkle,             (0.3, 0.3, 0.3)
effect_gate_selected:      mmu_static_blue,         (0, 0, 1)
effect_gate_available:     mmu_static_white_dim,    (0.3, 0.3, 0.3)
effect_gate_available_sel: mmu_ready_white,         (0.75, 0.75, 0.75)
effect_gate_unknown:       mmu_static_orange,       (0.5, 0.2, 0)
effect_gate_unknown_sel:   mmu_ready_orange ,       (0.75, 0.3, 0)
effect_gate_empty:         mmu_static_black,        (0, 0, 0)
effect_gate_empty_sel:     mmu_ready_red,           (0.2, 0, 0)

```

### Update mmu/addons/mmu_eject_buttons_hw.cfg
**Step 1: Clear the mmu_eject_buttons_hw.cfg file.** <br/><br/>
Start by completely deleting the content of that file and hitting save.

**Step 2: Paste the below configuration in the mmu_eject_buttons_hw.cfg file**<br/><br/>
The below starter setup is for an 8 lane unit. To set up a lower lane count, paste the complete content below and delete the corresponding `[gcode_button mmu_eject_button_N]` sections. If you have more than 8 lanes, add more blocks following the patterns below.
```
[gcode_button mmu_eject_button_0]
pin: mmu0:EJECT_BUTTON
press_gcode: _MMU_EJECT_BUTTON GATE=0

[gcode_button mmu_eject_button_1]
pin: mmu1:EJECT_BUTTON
press_gcode: _MMU_EJECT_BUTTON GATE=1

[gcode_button mmu_eject_button_2]
pin: mmu2:EJECT_BUTTON
press_gcode: _MMU_EJECT_BUTTON GATE=2

[gcode_button mmu_eject_button_3]
pin: mmu3:EJECT_BUTTON
press_gcode: _MMU_EJECT_BUTTON GATE=3

[gcode_button mmu_eject_button_4]
pin: mmu4:EJECT_BUTTON
press_gcode: _MMU_EJECT_BUTTON GATE=4

[gcode_button mmu_eject_button_5]
pin: mmu5:EJECT_BUTTON
press_gcode: _MMU_EJECT_BUTTON GATE=5

[gcode_button mmu_eject_button_6]
pin: mmu6:EJECT_BUTTON
press_gcode: _MMU_EJECT_BUTTON GATE=6

[gcode_button mmu_eject_button_7]
pin: mmu7:EJECT_BUTTON
press_gcode: _MMU_EJECT_BUTTON GATE=7
```

### Upload the emu_macros.cfg file and reference it in your printer.cfg
The [linked file here](https://github.com/DW-Tas/EMU/tree/main/macros) contains a set of configurations and definitions that are required for EMU to function. In addition, it contains a fan auto control macro, to minimize noise and ensure adequate unit cooling.

Upload that file in your klipper environment and add the below line to include it in your printer.cfg file:
```[include emu_macros.cfg]```

That file contains the **BME temperature and humidity sensor definitions** as below. It is set up for an 8 lane unit, so if you have less lanes, delete the corresponding blocks from the file.
```
[temperature_sensor Lane_N]
sensor_type: BME280
i2c_address: 118
i2c_mcu: mmu0  # mmu0=First lane, mmu1=second lane etc.
i2c_software_scl_pin: mmu0:PB3
i2c_software_sda_pin: mmu0:PB4
```
It also contains the definition of the onboard EBB temperature sensors used to control the unit fans. Similarly, it is set up for an 8 lane unit, so if you have less lanes, delete the corresponding blocks from the file.
```
[temperature_sensor _Lane_N_onboard]
sensor_type: temperature_mcu
sensor_mcu: mmu0 # mmu0=First lane, mmu1=second lane etc.
min_temp: 0
max_temp: 130
```
In addition, it contains the fan definitions for the unit as below. Similarly, it is set up for an 8 lane unit, so if you have less lanes, delete the corresponding blocks from the file.
```
[fan_generic _emu_fan_N]
pin: mmu0:MMU_FAN # mmu0=First lane, mmu1=second lane etc.
max_power: 1
kick_start_time: 0.5
```
Finally it contains the fan control macro that controls the fans on a by-lane basis. In the variable_sensors add the names of the **_Lane_N_onboard temperature sensors**, separated by a comma. In the variable_fans add the names of the **base unit fans**, separated by a comma. 

> [!NOTE]
> Prefixing the fans and board temperature sensors with a _ will hide them from the Mainsail UI, which is helpful to reduce clutter once you have your setup tuned and validated.

> [!IMPORTANT]
> The length of these two lists must match and correspond to each other (ie lane 0 fan and lane 0 onboard temp sensor must be first on the list etc).
> Make sure you include the **onboard temperature sensors in the fan control macro, not the BME sensors!**

Finally you can set the temperature where the fans turn on and off. By default, they are set to turn on at 39C and turn off at 37C.

```[gcode_macro MMU_FAN_CFG]
description: Holds configuration/state for multi fan controller.
variable_on_temp: 39.0
variable_off_temp: 37.0
variable_poll_s: 5.0
variable_enabled: True
variable_forced: -1                 # -1=AUTO, 0=all OFF, 1=all ON (global)
variable_sensors: "_Lane_0_onboard,_Lane_1_onboard,_Lane_2_onboard,_Lane_3_onboard,_Lane_4_onboard,_Lane_5_onboard,_Lane_6_onboard,_Lane_7_onboard"   # Comma-separated temperature_sensor names
variable_fans:    "_emu_fan_0,_emu_fan_1,_emu_fan_2,_emu_fan_3,_emu_fan_4,_emu_fan_5,_emu_fan_6,_emu_fan_7"  # Comma-separated fan_generic names
variable_warned_len_mismatch: False # internal: warn once per enable
gcode:
```
That file also contains some bespoke LED effects for the EMU, which are used earlier in the LED setup section.

### Save, restart and confirm lanes are visible
Once all of the above steps are completed hit save and restart klipper. The MMU hardware should now all be set up and all your lanes visible in the machine panel as below:

<p align="center">
  Installer screen
</p>

## Configuring Happy Hare parameters
Now that the hardware is set up and visible to klipper, the next step is to configure the Happy Hare software to match the EMU capabilities and general Type B MMU good practice. That configuration will be predominately done in the mmu/base/mmu_parameters.cfg file. The indicated configuration below is geared towards reliability of feeding vs. filament swap speed. Use that as a starting point and tune to your liking once the unit is fully configured and operational.

### Setting up the EMU software parameters in mmu/base/mmu_parameters.cfg
Unlike the hardware setup files, do not delete the content of this file. We will be making targeted changes to match the EMU capabilities as validated through our testing.

**MMU Hardware Limits:** The EMU can operate up to a maximum of 500mm/sec feeding velocity and 400mm/sec2 acceleration. Adjust the maximum hardware limits as below.</br>
```
gear_max_velocity: 500
gear_max_accel: 400
```
**Logging:** Reduce log verbosity to reduce SD Card wear and system load</br></br>
```
log_level: 1
log_file_level: 1		
log_statistics: 0 		
log_visual: 1			
log_startup_status: 1		
log_m117_messages: 1
```			
**Speeds:** Our objective is reliability with operation. While the EMU can operate at 500mm/sec feeding, any snag in the filament path risks the lane stepper skipping steps. As such, it is recommended that conservative values are used in the speed set up, and tune up from there.</br>
```
gear_from_spool_speed: 250
gear_from_spool_accel: 120
#gear_from_buffer_speed: 250 # This is not necessary. Delete this line as there is no buffer.
#gear_from_buffer_accel: 120 # This is not necessary. Delete this line as there is no buffer.
gear_unload_speed: 250
gear_unload_accel: 120

gear_short_move_speed: 100
gear_short_move_accel: 100
gear_short_move_threshold: 100
gear_homing_speed: 100

extruder_load_speed: 16
extruder_unload_speed: 20
extruder_sync_load_speed: 16
extruder_sync_unload_speed: 20
extruder_homing_speed: 16

macro_toolhead_max_accel: 0
macro_toolhead_min_cruise_ratio: 0.5
```
**Gate load:** The EMU uses the post stepper (gear) switch sensor as the filament homing point for the lanes. That means that when swapping colors, the filament will retract all the way into the EMU dry box. This has three benefits which maximise flexibility in lane / base unit arrangements and reliability in feeding filament:
1. The filament is kept as dry as possible as it is now fully in the dry box. This results in lower probability of the filament snapping in the lane stepper gear due to it absorbing humidity from the environment.
2. There is no need for a sensor at the combiner, simplifying wiring setup and configuration.
3. You can expand to as many lanes as you want with any combination of passive combiners to bring the lane bowden tubes together to one that feeds the toolhead.

The downside is that the full bowden length needs to be traversed when loading, resulting in slightly longer loading times (however that is almost insignificant) and that the bowden length for each lane needs to be calibrated before first use (this is an automated process described later in this guide).

In addition, conservative homing max and preload homing max value have been selected, to allow the user time to load the filament and ensure it is gripped by the EMU lane stepper. 

It is therefore recommended to use the below values as is and do not modify unless trying to troubleshoot a specific issue.</br>
```
gate_homing_endstop: mmu_gear	
gate_homing_max: 600
gate_preload_homing_max: 600
gate_preload_parking_distance: 1
gate_unload_buffer: 100
gate_parking_distance: 1          # park the filament 1mm before the stepper exit switch. Do not increase this value beyond this as you are then risking the filament walking past the stepper gears.
gate_autoload: 1
gate_final_eject_distance: 100
```
**Bowden load:** As the EMU can accomodate long bowden tubes feeding to the printer, the bowden_homing_max is increased to allow Happy Hare to feed a longer run. 

In addition the correction and unload test moves are disabled as the encoder is not fitted in the base setup. From experience, encoders tend to accumulate dust after a few thousand swap cycles requiring ongoing maintenance. In addition they materially elevate the noise profile of the unit and add a point of "filament impact" in the bowden loading path.</br>
```
bowden_homing_max: 3000	# if the EMU lane to toolhead distance is larger than 3 meters, increase this value.

bowden_apply_correction: 0	
bowden_allowable_load_delta: 10.0

bowden_pre_unload_test: 0	
bowden_pre_unload_error_tolerance: 60 
```
**Extruder homing:** The below values are tuned to improve overall feeding reliability. The extruder homing max value has been increased, allowing for slight slippage during the bowden load to be compensated for. In addition, the homing buffer has been increased reducing the fast load speed 50mm before the filament arrives at the toolhead, to reduce possibility of filament impacting the gears.</br>
```
extruder_homing_max: 400			# Larger than the default HH value. This allows for homing to complete even if the filament skips steps during the load/
extruder_homing_endstop: extruder	
extruder_homing_buffer: 50
extruder_collision_homing_current: 100

extruder_force_homing: 0
```
**Toolhead Load:** This section needs to be populated following toolhead dimension calibration. Starter values from the community are available here: https://link.3dcoded.xyz/tipconfigs/ . 

In addition, the below settings have been adjusted to allow more tolerance in case of the extruder delaying grabbing the filament, which improves feeding reliability and allows for more "flex" in a slightly miss-tuned setup</br>
```
toolhead_homing_max: 250			# Increased from default of 40, to allow more tolerance in the extruder not grabbing the filament immediately.
toolhead_unload_safety_margin: 90	# Increased from the default of 10, to ensure filament is for sure clear of the extruder during unload.
toolhead_post_load_tighten: 0		# this is ignored as EMU is a Type B MMU - set to 0
toolhead_post_load_tension_adjust: 1	# Adjust tension post load to attemt to centre the sync feedback sensor. 
toolhead_entry_tension_test: 0		# Not required - toolhead sensor ensures feeding has happened.
```
**Tip Forming:** A toolhead cutter is highly recommended. Venture into tip forming at your own risk!</br>
```
force_form_tip_standalone: 1		  # Always standalone tip forming (TURN SLICER OFF!)
form_tip_macro: _MMU_CUT_TIP	
extruder_form_tip_current: 130		  # Bump up extruder current during tip forming. Helps ensure no skipped steps on the extruder if cutting is not 100% clean
slicer_tip_park_pos: 0			      # This specifies the position of filament in extruder after slicer completes tip forming. (TURN SLICER TIP FORMING OFF!)
```
**Purging:** If you have the blobifier set up, enable it here. For a baseline, starter setup, the below is recommended. Setting up the blobifier is recommended to be done after this guide is complete and your first test print is completed successfully.</br>
```
force_purge_standalone: 0 		# Use slicer purging (purge block) - set to 1 for blobifier
purge_macro: 			            # Replace this with BLOBIFIER when set up. Leave empty if not using the blobifier. 
extruder_purge_current: 100		# leave this unchanged. If the extruder is skipping during purging with the blobifier you are most likely exceeding your hotend flow limit.
```
**Motor sync:** Setup sync feedback sensor (EMUSync) here. The sync multiplier high and low values allow for +/- 10% tolerance in rotation distance variation between your EMU lane and your extruder. If you find you need more than this for the unit to stay in sync then most likely either your extruder or EMU lane is not calibrated correctly.</br>
```
sync_gear_current: 50			    # 50% EMU stepper current during printing -> ~0.4A when printing. Higher than 0.5A can cause PLA to clog the EMU stepper in hot environments.
sync_feedback_enabled: 1		    # Enable EMU Sync sync feedback sensor
sync_feedback_buffer_range: 12		# EMU Sync switch to switch distance
sync_feedback_buffer_maxrange: 25	# EMU Sync max travel
sync_multiplier_high: 1.10		    # over-feed by 10% when in tension
sync_multiplier_low: 0.90		    # under-feed by 10% when in compression
```
**Filament Management:** Disable clog detection (as the encoder is not fitted to the unit) and enable endless spool (automated failover to the next available spool as defined in the gate map, administered via the Mainsail UI or Klipperscreen).</br>
```
enable_clog_detection: 0		
enable_endless_spool: 1			    # enable endless spool
endless_spool_on_load: 0	
endless_spool_eject_gate: -1		# Eject filament in the current gate
```
Here you can also configure spoolman filament management (highly recommended - instructions here:https://github.com/moggieuk/Happy-Hare/wiki/Spoolman-Support). </br></br>

**Calibration:** While happy hare can auto calibrate both the bowden tube length and lane rotation distance, I personally recommend a manual calibration for run to run consistency. Therefore all automated calibrations are disabled to ensure run-to-run consistency.</br>
```
autocal_bowden_length: 0	# Disable automated bowden length calibration
autotune_bowden_length: 0	# Disable automated bowden length tuning
skip_cal_rotation_distance: 0	# Require gate rotation distance calibration
autotune_rotation_distance: 0	# Disable automated gate calibration/tuning.
skip_cal_encoder: 0		# Encoder not fitted
autotune_encoder: 0		# Encoder not fitted
```

**Misc:** Minor options tuning and instructing Happy Hare that a filamentalist rewinder is used instead of a buffer </br>
```
timeout_pause: 86400		    # Idle time out in seconds. Set to 24 hours, to allow you to react and fix a pause if a swap issue materialises.
disable_heater: 60		        # Disable the hotend heater 60 seconds after an error is detected to reduce oozing.
default_extruder_temp: 230	    # Default temperature for performing swaps and forming tips when not in print (overridden by gate map). 230C is a good all around temperature for most material types.
extruder_temp_variance: 30	    # When waiting for extruder temperature this is the +/- permissible variance in degrees (>= 1).

startup_home_if_unloaded: 0	    # 0 = do nothing
startup_reset_ttg_map: 0	    #  0 = do nothing
show_error_dialog: 0		    # 0 = show error in console only. No mainsail pop-up
preload_attempts: 5		        # How many "grabbing" attempts are made to pick up the filament with preload feature
strict_filament_recovery: 0	    # If enabled with MMU with toolhead sensor, this will cause filament position recovery to
                                # perform extra moves to look for filament trapped in the space after extruder but before sensor
                                # This is largely uncessary but can be enabled if your toolhead setup is not particularly reliable.
filament_recovery_on_pause: 1	# Run a quick check to determine current filament position on pause/error.
retry_tool_change_on_error: 1	# Automatically retry a failed tool change. While this may mask a unit issue, we are aiming for relability during print.
bypass_autoload: 1		        # If extruder sensor fitted, this controls the automatic loading of extruder for bypass operation
has_filament_buffer: 0          # We are using a Filamentalist so no separate filament buffer is installed
#
# Advanced options. Don't mess unless you fully understand. Read documentation.
#
encoder_move_validation: 0	     # ADVANCED: 1 = Normally Encoder validates move distances are within given tolerance
                                 #           0 = Validation is disabled (eliminates slight pause between moves but less safe)
print_start_detection: 1	     # ADVANCED: Enabled for Happy Hare to automatically detect start and end of print and call
                                 # ADVANCED: MMU_PRINT_START and MMU_PRINT_END automatically. Harmless to leave enabled but can disable
                                 #           if you think it is causing problems and known START/END is covered in your macros
extruder: extruder		         # ADVANCED: Name of the toolhead extruder that MMU is using
gcode_load_sequence: 0		     # VERY ADVANCED: Gcode loading sequence 1=enabled, 0=internal logic (default)
gcode_unload_sequence: 0	     # VERY ADVANCED: Gcode unloading sequence, 1=enabled, 0=internal logic (default)
```

**Klipper:** Enable klipper timer too close (TTC) mitigations.</br>
```
update_trsync: 1		    # 1 = Increase TRSYNC_TIMEOUT, 0 = Leave the klipper default
canbus_comms_retries: 3		# Number of retries. Recommend the default of 3.
update_bit_max_time: 1		# 1 = Increase BIT_MAX_TIME, 0 = Leave the klipper default
update_aht10_commands: 0	# BTT ViViD specific setting. Leave at 0.
```

### Setting up the EMU software parameters in mmu/base/mmu_macro_vars.cfg
Unlike the hardware setup files, do not delete the content of this file. The below are some common settings that I have found usefull to change from default. However, the **detailed guide on Happy hare must be followed to set up your cut tip macro and to configure the system for your specific printer setup**. For more read here: https://github.com/moggieuk/Happy-Hare/wiki/Configuring-mmu_macro_vars.cfg

> [!WARNING]
> **WARNING: DO NOT RUN A PRINT WITHOUT CONFIGURING THE ABOVE.** The stock cut tip macro will most likely not work for your setup and you will crash the hotend on the cutter.

```
variable_min_toolchange_z       : 15.0 # Be safe and dont scratch the bed
variable_park_travel_speed      : 450  # Travel a bit faster to avoid stringing
```

## Configuring PSF and Flowguard
EMU and Happy Hare supports using a [proportional sync feedback sensor](https://github.com/DW-Tas/EMU/tree/main/STL/Tension-compression-sensor/Proportional%20Sync%20Feedback%20(PSF)%20Version) to accurately measure filament tension in the bowden tube. This is used in place of and instead of the dual switch EMUSync. The sensor [is available to purchase from Aliexpress](https://www.aliexpress.com/item/1005010470743517.html).

The proportional sensor offers the below key advantages:
1. Real time tension/compression monitoring in the bowden tube
2. Precise syncronisation between the extruder and EMU steppers
3. Real time detection of both clogs and tangles

### PSF Configuration:
The sensor is plugged in [as per the wiring diagram](https://github.com/DW-Tas/EMU/tree/main/docs/assembly_wiring#wiring-instructions-and-diagrams) - ground and signal plug into the EBB thermistor port and 5V to any unused 5V pins on the EBB.

**Step 1:** Comment out or delete the below section in the mmu_hardware.cfg file: 
```
# sync_feedback_tension_pin: ^mmu0:MMU_TENSION         # Compression is when you pull the bowden tubes (entry/exit) away from each other. Tension when you push the tubes together.
# sync_feedback_compression_pin: ^mmu0:MMU_COMPRESSION
```

**Step 2:** Uncomment or add the below section right below in the mmu_hardware.cfg file:
```
# Section below if using the Proportional (PSF) version of the EMU Sync. Run the calibration routine (MMU_CALIBRATE_PSENSOR) and
# update the sync_feedback_analog_max_compression, sync_feedback_analog_max_tension and sync_feedback_analog_neutral_point accordingly.
# Comment out/delete the dual switch section above and uncomment the section below to use.
sync_feedback_analog_pin: mmu0:MMU_TH
sync_feedback_analog_max_compression: 0.9435
sync_feedback_analog_max_tension:     0.0982
sync_feedback_analog_neutral_point:   0.5275
```
**Step 3:** Restart and test the sensor. 
1. Pull the bowden tube and expand the EMUSync PSF sensor. While holding in the expanded position run the below macro in the printer console: `MMU_QUERY_PSENSOR`.
2. Compress the sensor by pushing the ends together and run the same macro again. Record both values.
> [!IMPORTANT]
> You should see a **max raw value** greater than ~0.9 and a **min raw value** or less than ~0.1. If the values do not change when expanding and compressing the sensor recheck your wiring!

**Step 4:** Set the EMUSync dimensions in the mmu_parameters.cfg file as below. Save and restart.
```
sync_feedback_enabled: 1		
sync_feedback_buffer_range: 16		# Travel in "buffer" between compression/tension or one sensor and end
sync_feedback_buffer_maxrange: 16	# Absolute maximum end-to-end travel (mm) provided by buffer
sync_feedback_speed_multiplier: 5	# % "twolevel" gear speed delta to keep filament neutral in buffer
sync_feedback_boost_multiplier: 3	# % "twolevel" extra gear speed boost for finding initial neutral position
sync_feedback_extrude_threshold: 5	# Extruder movement (mm) for updates
```

**Step 5:** Calibrate the sensor.
1. Load filament from any lane to the toolhead using a Tx (T0,T1 etc) command.
2. In the console run `MMU_CALIBRATE_PSENSOR`
3. Note down the produced values
> [!IMPORTANT]
> If the max and min values differ significantly (>0.1) from the min and max raw values above, your calibration has failed due to excess bowden tube slack or because the sensor is getting jammed due to excess friction. Validate that the sensor moves freely and run the calibration command as follows: `MMU_CALIBRATE_PSENSOR MOVE=50`

The produced values should look like the below:
```
sync_feedback_analog_max_compression: 0.9435
sync_feedback_analog_max_tension:     0.0982
sync_feedback_analog_neutral_point:   0.5275
```

Update the corresponding values in the mmu_hardware.cfg file, save and restart.

**Step 6:** Configure flowguard (clog/tangle detection) <br/>
Edit the mmu_parameters.cfg file and amend the values below to match the suggested configuration.

```
flowguard_enabled: 1	
flowguard_max_relief: 2
flowguard_encoder_mode: 0
```
Save and restart. 

**Step 7:** You can now start a print and test the sensor in a print
1. Start a print and monitor the flowguard value in the MMU panel. It should remain close to the neutral (0) threshold
2. Expand the sensor manually - flowguard should trigger a pause. Let go, and click resume. The print should continue uninterrupted.



### EMUSync PSF insights:
You can use the sync sensor to visualise your printer's extrusion consistency, checking whether you are pushing the hotend to its limits. To do so, enable logging `sync_feedback_debug_log: 1` in the mmu_parameters.cfg file and restart. Run a print and after it is complete, execute the below command in the printer shell `~/Happy-Hare/utils/plot_sync_feedback.sh ~/printer_data/logs/sync_5.jsonl` where sync_N being the lane number in use.

You can read more on how to interpret the sync feedback telemetry data in the [Happy Hare wiki](https://github.com/moggieuk/Happy-Hare/wiki/Synchronized-Gear-Extruder#interpreting-telemetry).

**Normal telemetry data with an "unstressed" hotend** </br>
Notice how the orange line is **pretty flat and consistent**. This indicates that there is very little dynamic variation during printing between the EMU and the extruder, meaning the extruder can maintain ideal flow easily throughout the print. Also how the blue line (EMU rotation distance) converges and stabilises fairly quickly to a perfectly stable value.</br></br>


**Telemetry data showing a tangle developing towards the end of the print** </br>
Notice how the orange and blue lines slowly creep away from neutral and then flowguard (red vertical line) triggers saving the print.</br></br>
T2 sim_plot

**Telemetry data showing a hotend that is struggling to keep up with flow when printing at higher flow rates** </br>
Notice how the blue line (RD) and orange line (sensor position) rapidly deviate from neutral when an object with high flow rate is printed.</br></br>


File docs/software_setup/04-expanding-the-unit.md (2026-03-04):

# EMU Happy Hare Hardware and Software Setup Guide

This is a provisional sofware setup guide for the EMU using Happy Hare v3. This guide is meant to be read in conjunction with the Happy Hare setup guide as found here: https://github.com/moggieuk/Happy-Hare/wiki

## Table of Contents

- [Expanding the unit with more lanes](#expanding-the-unit-with-more-lanes)

## Expanding the unit with more lanes
Beyond the electrical connections, the below steps need to be undertaken when adding additional lanes to the EMU unit.

**mmu.cfg**

Add an additional MCU block for each new lane:
```
[mcu mmuN]
canbus_uuid: UUID 
canbus_interface: can0
```

Add the additional mmu board to the board pins section:
```
[board_pins mmu]
mcu: mmu0, mmu1, mmu2, mmu3, mmu4, mmu5, mmu6, mmuN
aliases:
    MMU_GEAR_UART=PA15,
    MMU_GEAR_STEP=PD0,
    MMU_GEAR_DIR=PD1,
    MMU_GEAR_ENABLE=PD2,
    MMU_GEAR_DIAG=,
    MMU_NEOPIXEL=PD3,
    MMU_NEOPIXEL_LOGO=,
    MMU_PRE_GATE=PB7,
    MMU_POST_GEAR=PB5,
    MMU_TENSION=PB8,
    MMU_COMPRESSION=PB9,
    MMU_TH=PA3,
    MMU_FAN=PA0,
    EJECT_BUTTON=PB6,
```

**mmu_hardware.cfg:**

Update the below to reflect your current lane count:
```
[mmu_machine]
num_gates: 8
```
Add the additional environment sensors block.
```
environment_sensors:   temperature_sensor Lane_0,
						temperature_sensor Lane_1,
                        temperature_sensor Lane_2,
                        temperature_sensor Lane_3,
                        ...
                        temperature_sensor Lane_N
```
Add additional stepper definitions, where N is the lane number:
```
...
[tmc2209 stepper_mmu_gear_N]
uart_pin: mmuN:MMU_GEAR_UART_N

[stepper_mmu_gear_N]
step_pin: mmuN:MMU_GEAR_STEP_N
dir_pin: mmuN:MMU_GEAR_DIR_N
enable_pin: !mmuN:MMU_GEAR_ENABLE_N
...
```

Define the additional pre-gate and post gear sensors (pre-stepper, post-stepper)
```
[mmu_sensors]
...
pre_gate_switch_pin_N: ^mmuN:MMU_PRE_GATE
post_gear_switch_pin_N: ^mmuN:MMU_POST_GEAR
...
```

Add another neopixel LED's block
```
[neopixel mmuN_leds]
pin: mmuN:MMU_NEOPIXEL
chain_count: 2			
color_order: GRBW	
```

Update the mmu_led's entry and exit LED numbers
```
[mmu_leds unit0]
exit_leds:
  neopixel:mmu0_leds (1) # add/remove to match number of lanes
  neopixel:mmu1_leds (1)
  neopixel:mmu2_leds (1)
  neopixel:mmu3_leds (1)
  neopixel:mmu4_leds (1)
  neopixel:mmu5_leds (1)
  neopixel:mmu6_leds (1)
  ...
  neopixel:mmuN_leds (1)
entry_leds:
  neopixel:mmu0_leds (2) # add/remove to match number of lanes
  neopixel:mmu1_leds (2)
  neopixel:mmu2_leds (2)
  neopixel:mmu3_leds (2)
  neopixel:mmu4_leds (2)
  neopixel:mmu5_leds (2)
  neopixel:mmu6_leds (2)
  ...
  neopixel:mmuN_leds (2)
frame_rate: 24
```

**mmu_eject_buttons_hw.cfg**

Define the additional eject buttons in the mmu_eject_buttons_hw.cfg file:
```
[gcode_button mmu_eject_button_N]
pin: mmuN:EJECT_BUTTON
press_gcode: _MMU_EJECT_BUTTON GATE=N
```

**mmu_macro_vars.cfg:**

Add an additional tool change gcode macro at the end of the file for each new lane:
```
[gcode_macro TN]
gcode: MMU_CHANGE_TOOL TOOL=N
```

**emu_macros.cfg**

Add additional temperature sensor, fan and BME sensor definitions and update the custom fan control macro to use them

Finally dont forget to execute the 2 calibrations for the new lanes - MMU_CALIBRATE_BOWDEN and  MMU_CALIBRATE_GEAR as descibed in the calibration section.

```
[temperature_sensor Lane_N]
sensor_type: BME280
i2c_address: 118
i2c_mcu: mmuN
i2c_software_scl_pin: mmuN:PB3
i2c_software_sda_pin: mmuN:PB4

[temperature_sensor _Lane_N_onboard]
sensor_type: temperature_mcu
sensor_mcu: mmuN
min_temp: 0
max_temp: 130

[fan_generic _emu_fan_N]
pin: mmuN:MMU_FAN
max_power: 1
kick_start_time: 0.5

[gcode_macro MMU_FAN_CFG]
...
variable_sensors: ".....,_Lane_N_onboard"
variable_fans:    "......,_emu_fan_N"
...
```

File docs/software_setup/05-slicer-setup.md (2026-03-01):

# Slicer setup and optimisation for multi color prints

Orca slicer is the recommended slicer for the EMU. The guide below will take you through a set of mandatory and recommended settings to help you achieve the best results possible from your EMU. The guide assumes that you are using a toolhead equipped with a cutter. Therefore all tip forming activity in the slicer will be disabled.

<p align="center">
  1 (4)
  1 (5)
  1 (2)
  1 (3)
</p>

## Table of Contents

- [Orca slicer mandatory setup](#orca-slicer-mandatory-setup)
  - [Machine G-Code setup](#machine-g-code-setup)
    - [Machine Start G-code](#machine-start-g-code)
    - [Machine End G-code](#machine-end-g-code)
    - [Layer change G-code](#layer-change-g-code)
    - [Change Filament G-code](#change-filament-g-code)
  - [Multi Material setup](#multi-material-setup)
  - [Extruder setup](#extruder-setup)
  - [Filament selection](#filament-selection)
- [Orca slicer profile tuning for multi-color printing](#orca-slicer-profile-tuning-for-multi-color-printing)
  - [Reducing color bleed](#reducing-color-bleed)
    - [Maximise the time spent printing hidden features before moving to the outer wall](#maximise-the-time-spent-printing-hidden-features-before-moving-to-the-outer-wall)
    - [Disable flush into objects' infill and support](#disable-flush-into-objects-infill-and-support)
    - [Use 3 (or more) walls](#use-3-or-more-walls)
    - [Use the blobifier](#use-the-blobifier)
    - [Tune your purge multiplier](#tune-your-purge-multiplier)
    - [Increase your variable_retract_length (mmu_macro_vars.cfg)](#increase-your-variable_retract_length-mmu_macro_varscfg)
  - [Optimising Print Quality](#optimising-print-quality)
    - [Speed settings](#speed-settings)
    - [Quality settings](#quality-settings)

## Orca slicer mandatory setup

### Machine G-Code setup
#### Machine Start G-code:
The Orca Slicer print start gcode is required to be amended to include the below additions. 
```
MMU_START_SETUP INITIAL_TOOL={initial_tool} TOTAL_TOOLCHANGES=!total_toolchanges! REFERENCED_TOOLS=!referenced_tools! TOOL_COLORS=!colors! TOOL_TEMPS=!temperatures! TOOL_MATERIALS=!materials! FILAMENT_NAMES=!filament_names! PURGE_VOLUMES=!purge_volumes!
MMU_START_CHECK
PRINT_START HOTEND=[nozzle_temperature_initial_layer] BED=[bed_temperature_initial_layer_single] CHAMBER=[chamber_temperature]
MMU_START_LOAD_INITIAL_TOOL
SET_PRINT_STATS_INFO TOTAL_LAYER={total_layer_count} ; For pause at layer functionality and better print stats
```
> [!WARNING]
> Replace the print start line with your existing print start command!

#### Machine End G-code:
The Orca Slicer print end gcode is required to be amended to include the below additions. 
```
MMU_END
PRINT_END ; your existing print end macro
```
> [!WARNING]
> Replace the print end line with your existing print end command!

#### Layer change G-code
**After Layer change:**</br>
```
; ... your existing layer change G-code...
SET_PRINT_STATS_INFO CURRENT_LAYER={layer_num + 1}
_MMU_UPDATE_HEIGHT
```

#### Change Filament G-code
If using a purge block set up:
```
T[next_extruder]
```
If you have the blobifier add-on set up, add the below change filament g-code. This will enable purge volume reporting in the slicer. Also the retraction command is necessary to avoid double de-retracting and oozing on the prime tower.
```
T[next_extruder]
G1 E-{old_retract_length} F3000
; FLUSH_START
; EXTERNAL_PURGE {flush_length}
; FLUSH_END
```

### Multi Material setup
Ensure that in the Multi Material tab, the below settings are set up:
1. Single Extruder Multi Material = selected
2. Extruders = 1
3. Manual Filament Change = de-selected
4. Purge in prime tower = selected. Deselect only if using the blobifier or similar purging system
5. Enable filament ramming = de-selected
6. Single extruder multi-material parameters - all set to 0 and high extruder current on filament swap = de-selected
7. Set up the advanced section with the approximate filament swap times - you can get these by typing MMU_STATS in the printer console after you have successfully ran a few multi-color prints

**No blobifier:**
<p align="center">
  
</p>

**With the blobifier:**
<p align="center">
  
</p>

### Extruder setup
Ensure that in the Extruder tab, the below settings are set up:
1. Retraction when switching material = 0

<p align="center">
  
</p>

### Filament selection
Using the (+) button, add as many filaments as available lanes in your EMU. 

<p align="center">
  
</p>

## Orca slicer profile tuning for multi-color printing

### Reducing color bleed
One of the biggest downsides to multi-color printing with a single nozzle is **the potential for color bleed**. This is usually the case when:
1. When swapping from **high saturation colors (red, black) to white**
2. Combined with **too low of a purge volume**
3. And using a **long meltzone hotend**

This happens due to the **molten material sticking to the hotend melt zone** and requiring disproportional amount of filament to "disrupt" that boundary layer and flush the color through. This is made worse by the fact that **filament flows in a laminar way**, hence there is little to no "turbulance" in the hotend to disrupt that layer.. 

Ways to mitigate include:
1. Use a regular flow (not a CHT) nozzle. The extra filament channels multiply the surface area that the boundary layer can be created against
2. Use a small meltzone nozzle. For multi-color printing, the vast majority of print time is spent swapping filaments and purging. Hence a lower flow hotent will not impact overall print speed by a significant factor

In addition to the above physical changes, the **below slicer settings can help** contain the color bleed

#### Maximise the time spend printing hidden features before moving to the outer wall
1. Enable Inner Outer Inner wall ordering mode.
2. Enable print infill first.
Printing **infill first results in the printer spending more time printing inside the model** before transitioning to the visible surfaces of the model (outer wall). It, therefore, increases the amount of filament extruded before the outer walls are printed and the probability that the outer walls will not show color bleed. **Inner Outer Inner wall ordering hides the resulting artefacts** from printing infill first.

For comparison, outer inner wall ordering mode must be avoided as it will print the external facing walls first, immediately after a color change!

<p align="center">
  
</p>

#### Disable flush into objects' infill and support
Similarly to the point above, disabling these settings ensures that **your defined purge volume is spent outside the model**.

<p align="center">
  
</p>

#### Use 3 (or more) walls
As above, the more walls printed before the outer perimeter, the higher the chance that the external walls are printed without color bleed.

<p align="center">
  
</p>

#### Use the blobifier
The blobifier algorithm **executes purging with varying speeds**, which helps **disrupt the laminar flow** of the filament against the walls. If your printer can accomodate the blobifier setup, it is strongly recommended that you set it up.

<p align="center">
  
</p>

In the picture above, you can see the no color bleed transition between white and black on the same layer. In addition you can observe the "ripples" created on the purge blobs due to the blobifier varying the purge speed and retracting and de-retracting during the purge, to flush out the filament from the nozzle.

> [!NOTE]
> If you are using the blobifier **do not disable the prime tower**. The prime tower will not be used to "purge" filament, rather **re-prime the nozzle**, clear out any air bubbles in the hotend that may have occured during the purge process and equalize nozzle pressure before resuming printing on the model. <br/>
> Set the prime volume to be equal to your meltzone volume **(meltzone length in mm * 2.4)**

<p align="center">
  
</p>

#### Tune your purge multiplier
Reducing the purge multiplier to 0.8-0.7 will indeed save some purge material; however more likely than not (unless you are using a particularly small meltzone hotend) it will result in color bleed. Now depending on how clean you want your prints to look, a purge multiplier of 1.2-1.25 (or more) is not unusual.

<p align="center">
  
</p>

> [!NOTE]
> Make sure your **nozzle volume is accurately set in the slicer** settings!

<p align="center">
  
</p>

#### Increase your variable_retract_length (mmu_macro_vars.cfg)
Reducing the amount of left over filament in the hotend can help reduce slightly the amount of material needing to be purged. I**ncreasing the variable_retract_length value to be ~5-10mm less than the variable_blade_pos** is recommended. 

> [!IMPORTANT]
> Make sure you **enable variable_simple_tip_forming**. It reduces the probability of clogs at the hotend when performing large retractions!<br/>
> Also make sure your variable_pushback_length plus toolhead_ooze_reduction is a mm or two less than your variable_retract_length.<br/>
> <br/>
> If you get persistent clogging with the above mitigations enabled, reduce your variable retract length until it stops. Proportionally also reduce the push back length (even though too large values there will be ignored, however update for configuration correctness)

### Optimising Print Quality
As the vast majority of the time during multi-color printing is spent in tool swapping, you can afford to set conservative print settings which can materially improve the produced output with very little time tradeoff.

The below are my preferred settings for multi-color printing.

**Speed settings:**
<p align="center">
  1 (4)
  1 (5)
</p>

**Quality settings:**
<p align="center">
  1 (4)
  1 (5)
  1 (5)
</p>

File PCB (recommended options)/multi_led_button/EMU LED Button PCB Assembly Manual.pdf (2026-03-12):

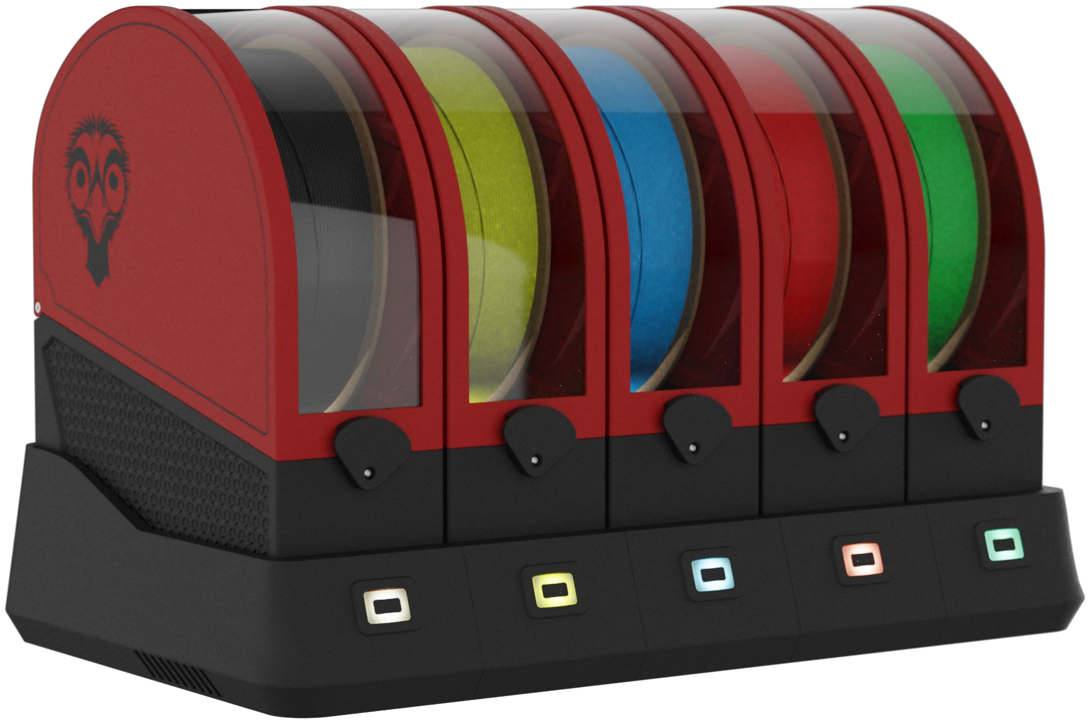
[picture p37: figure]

# EMU LED Button PCB Assembly Manual

### EMU - The Expandable Multi material Unit

VERSION 2026-03-11

INTRODUCTION | WWW.DWTAS.NET

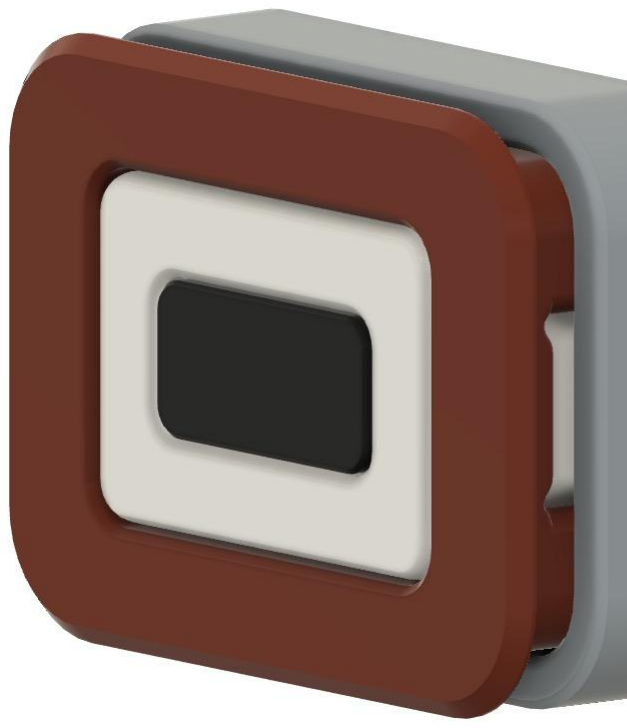
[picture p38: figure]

2

PART PRINTING GUIDELINES
To have the best chance of success, the following print settings are highly recommended.

3D PRINTING PROCESS
Fused Deposition Modeling (FDM)

INFILL TYPE
Gyroid or Cubic

MATERIAL
ABS/ASA. Glass and CF filled material are compatible.
Use natural ABS for the diffuser.

INFILL PERCENTAGE
Recommended: 15%

LAYER HEIGHT
Mandatory: 0.2mm, including first layer!

WALL COUNT
Recommended: 4

EXTRUSION WIDTH
0.4mm, Arachne slicing engine. Infill can be printed wider (0.45/0.48) to increase layer bonding.

SOLID TOP/BOTTOM LAYERS
Recommended: 5

2

ASSEMBLING THE PCB | WWW.DWTAS.NET

Depending on your source, the LED board may require you to solder the 5 pin JST connector. Preheat your soldering iron to 320C, flow some solder on the iron tip to ensure its clean, insert and solder the connector.

CAUTION:
Be mindful when soldering to not touch the LEDs with a hot soldering iron, as they will melt!
Use a fine soldering tip to avoid colliding with the PCB parts.
Pay attention to the connector orientation!

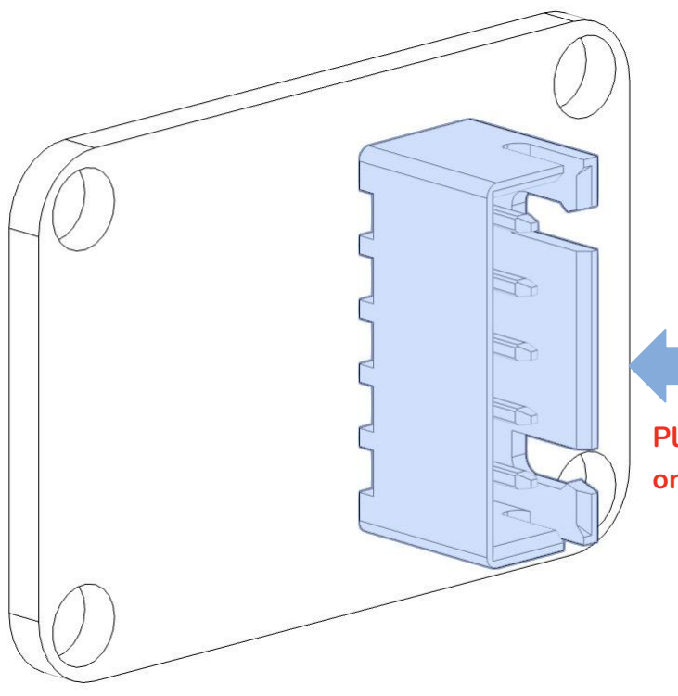
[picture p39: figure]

Place the JST connector
on the rear of the board

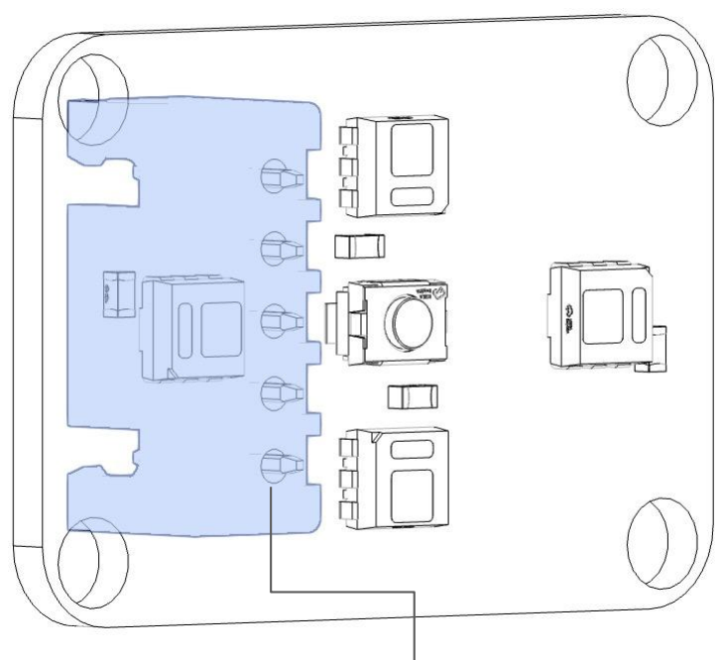
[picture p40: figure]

Solder all the JST pins to the board

LED BUTTON ASSEMBLY | WWW.DWTAS.NET

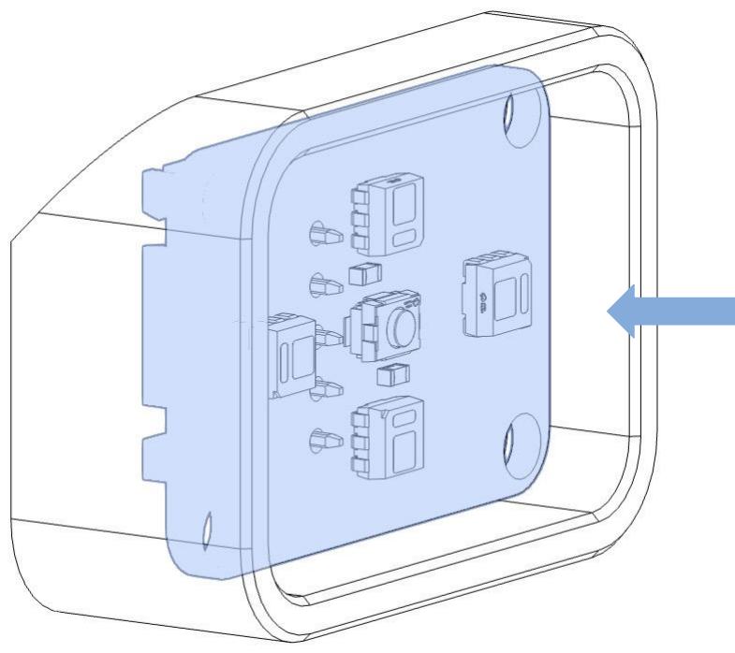
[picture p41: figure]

Place the LED Button PCB in the Button Rear assembly.

Make sure it sits flush with the rear surface.

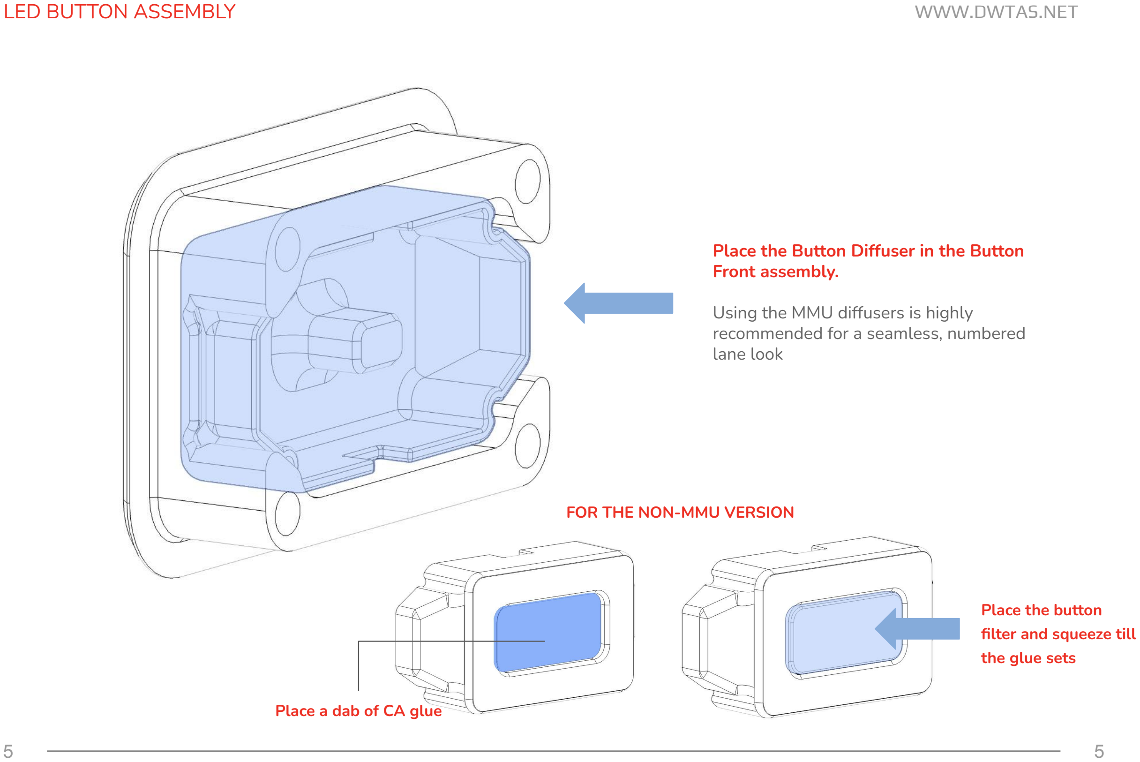
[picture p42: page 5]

LED BUTTON ASSEMBLY | WWW.DWTAS.NET

Place the Button Diffuser in the Button Front assembly.

Using the MMU diffusers is highly recommended for a seamless, numbered lane look

FOR THE NON-MMU VERSION

Place a dab of CA glue

Place the button
filter and squeeze till
the glue sets

LED BUTTON ASSEMBLY | WWW.DWTAS.NET

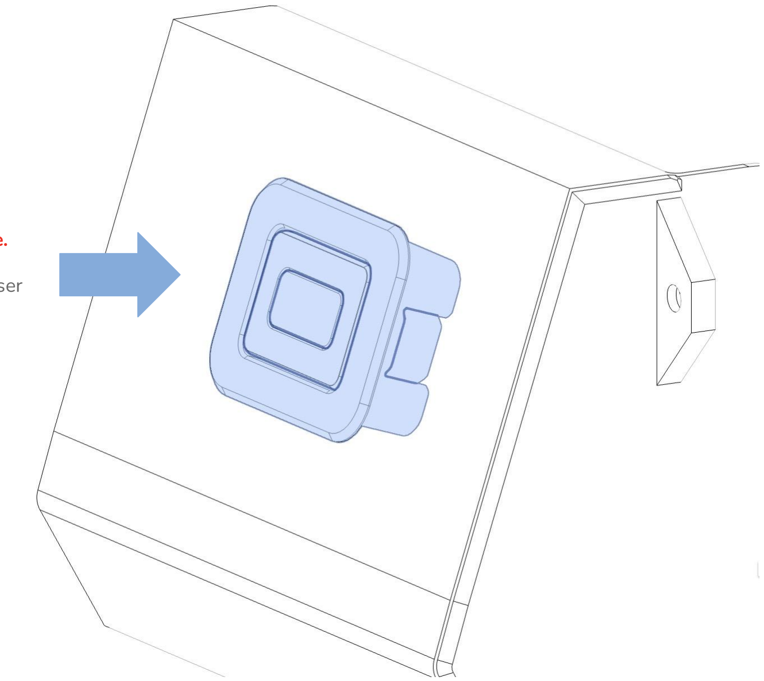
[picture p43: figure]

Place the front assembly in the base.

Tilt the base slightly so that the diffuser doesn’t fall out.

LED BUTTON ASSEMBLY | WWW.DWTAS.NET

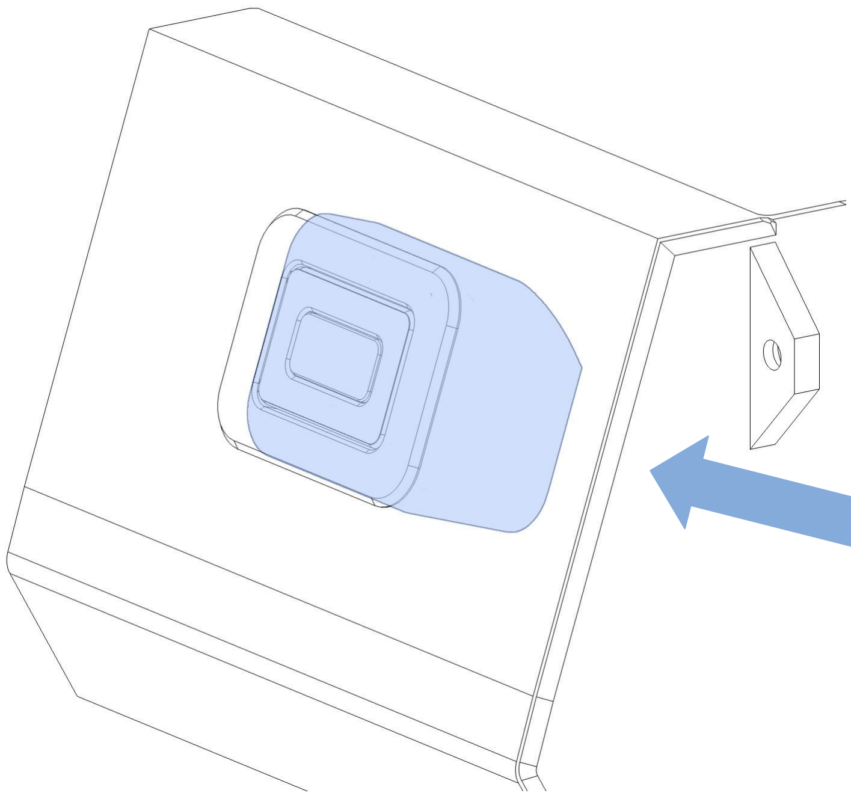
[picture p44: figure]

Place the rear of assembly in the base and squeeze the parts so they fully seat against each other.

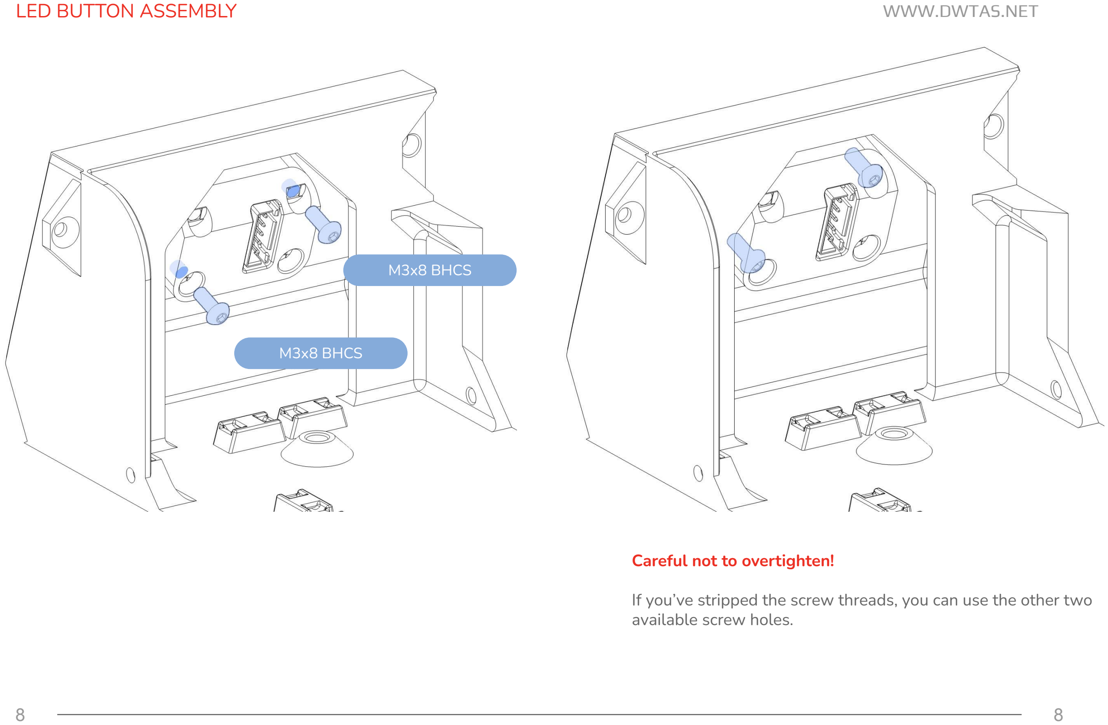
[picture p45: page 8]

LED BUTTON ASSEMBLY | WWW.DWTAS.NET

Careful not to overtighten!

If you’ve stripped the screw threads, you can use the other two available screw holes.

M3x8 BHCS

M3x8 BHCS

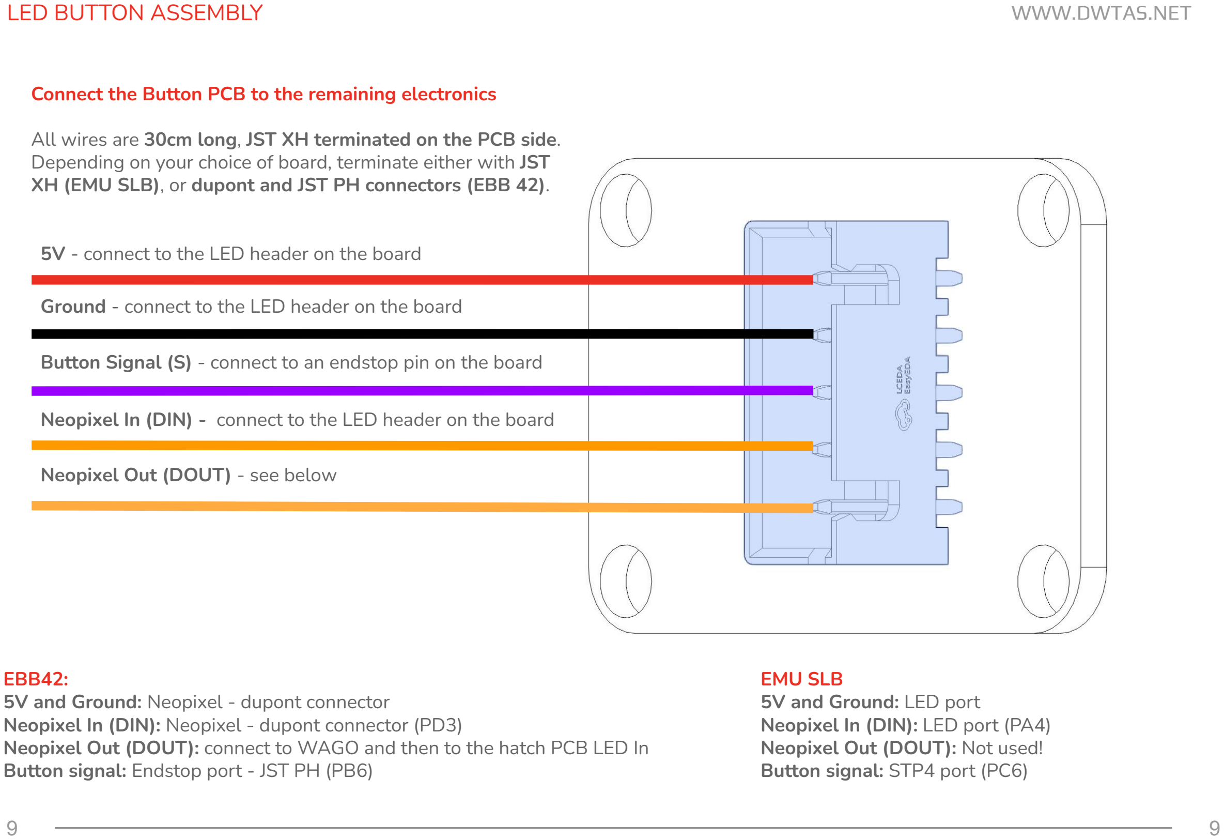
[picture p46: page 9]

LED BUTTON ASSEMBLY | WWW.DWTAS.NET

Connect the Button PCB to the remaining electronics

All wires are 30cm long, JST XH terminated on the PCB side. Depending on your choice of board, terminate either with JST XH (EMU SLB), or dupont and JST PH connectors (EBB 42).

5V - connect to the LED header on the board

Ground - connect to the LED header on the board

Button Signal (S) - connect to an endstop pin on the board

Neopixel In (DIN) - connect to the LED header on the board

Neopixel Out (DOUT) - see below

EBB42:
5V and Ground: Neopixel - dupont connector
Neopixel In (DIN): Neopixel - dupont connector (PD3)
Neopixel Out (DOUT): connect to WAGO and then to the hatch PCB LED In Button signal: Endstop port - JST PH (PB6)

EMU SLB
5V and Ground: LED port
Neopixel In (DIN): LED port (PA4) Neopixel Out (DOUT): Not used! Button signal: STP4 port (PC6)

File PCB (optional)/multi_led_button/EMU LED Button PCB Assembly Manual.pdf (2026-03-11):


# EMU LED Button PCB Assembly Manual

### EMU - The Expandable Multi material Unit

VERSION 2026-03-11

INTRODUCTION | WWW.DWTAS.NET

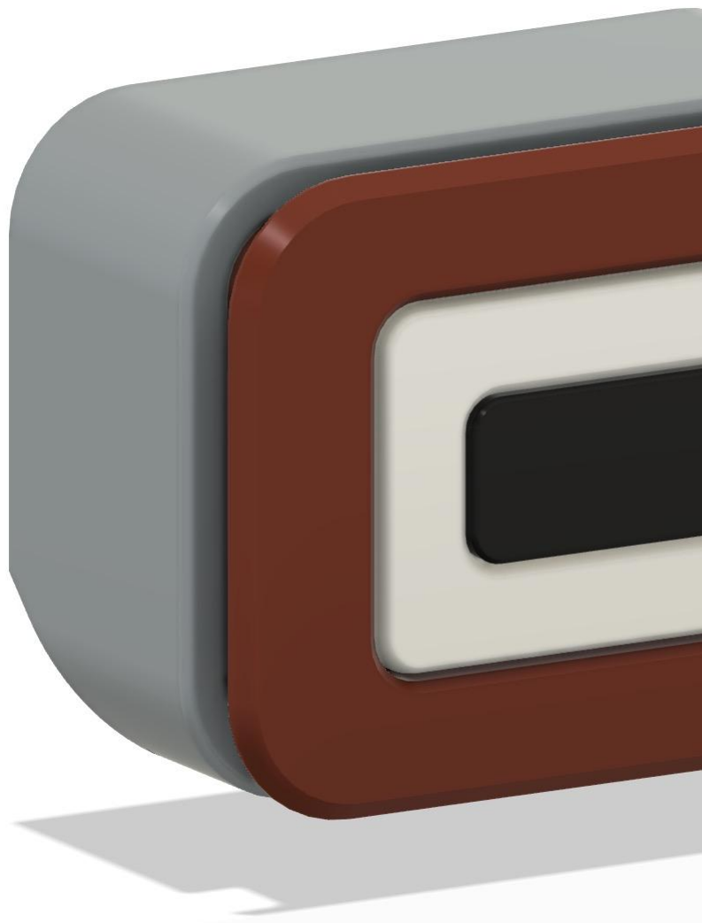
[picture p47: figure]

2

PART PRINTING GUIDELINES
To have the best chance of success, the following print settings are highly recommended.

3D PRINTING PROCESS
Fused Deposition Modeling (FDM)

INFILL TYPE
Gyroid or Cubic

MATERIAL
ABS/ASA. Glass and CF filled material are compatible.
Use natural ABS for the diffuser.

INFILL PERCENTAGE
Recommended: 15%

LAYER HEIGHT
Mandatory: 0.2mm, including first layer.

WALL COUNT
Recommended: 4

EXTRUSION WIDTH
0.4mm, Arachne slicing engine. Infill can be printed wider (0.45/0.48) to increase layer bonding.

SOLID TOP/BOTTOM LAYERS
Recommended: 5

2

ASSEMBLING THE PCB | WWW.DWTAS.NET

Depending on your source, the LED board may require you to solder the 5 pin JST connector. Preheat your soldering iron to 320C, flow some solder on the iron tip to ensure its clean, insert and solder the connector.

CAUTION:
Be mindful when soldering to not touch the LEDs with a hot soldering iron, as they will melt!
Use a fine soldering tip to avoid colliding with the PCB parts.
Pay attention to the connector orientation!


Place the JST connector
on the rear of the board


Solder all the JST pins to the board

LED BUTTON ASSEMBLY | WWW.DWTAS.NET

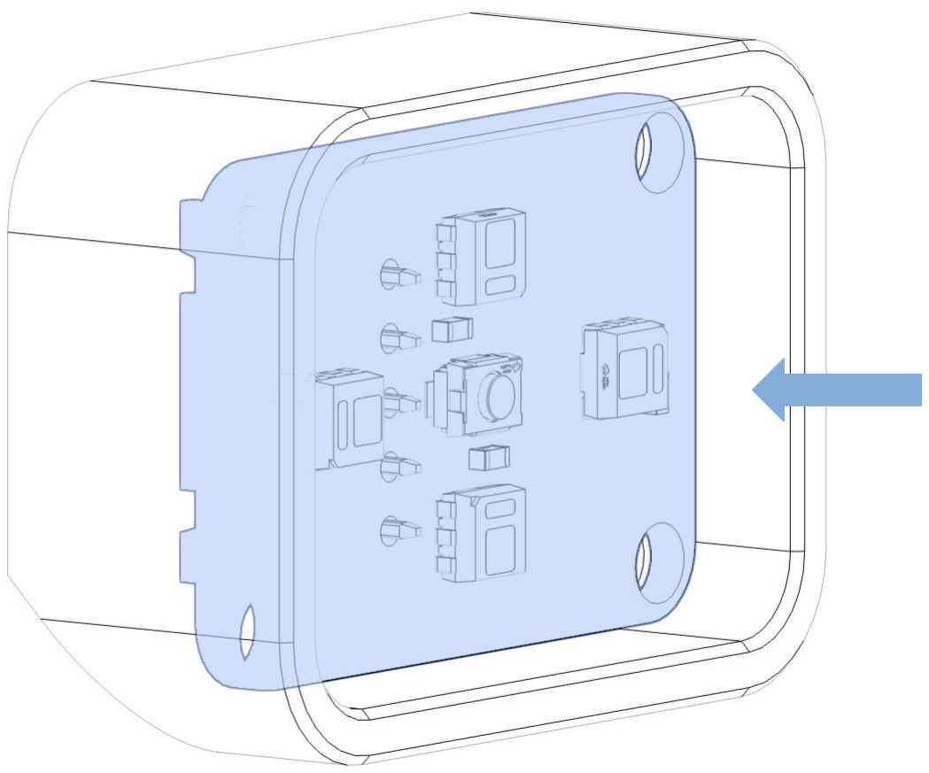
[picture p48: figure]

Place the LED Button PCB in the Button Rear assembly.

Make sure it sits flush with the rear surface.


LED BUTTON ASSEMBLY | WWW.DWTAS.NET

Place the Button Diffuser in the Button Front assembly.

Using the MMU diffusers is highly recommended for a seamless, numbered lane look

FOR THE NON-MMU VERSION

Place a dab of CA glue

Place the button
filter and squeeze till
the glue sets

LED BUTTON ASSEMBLY | WWW.DWTAS.NET


Place the front assembly in the base.

Tilt the base slightly so that the diffuser doesn’t fall out.

LED BUTTON ASSEMBLY | WWW.DWTAS.NET

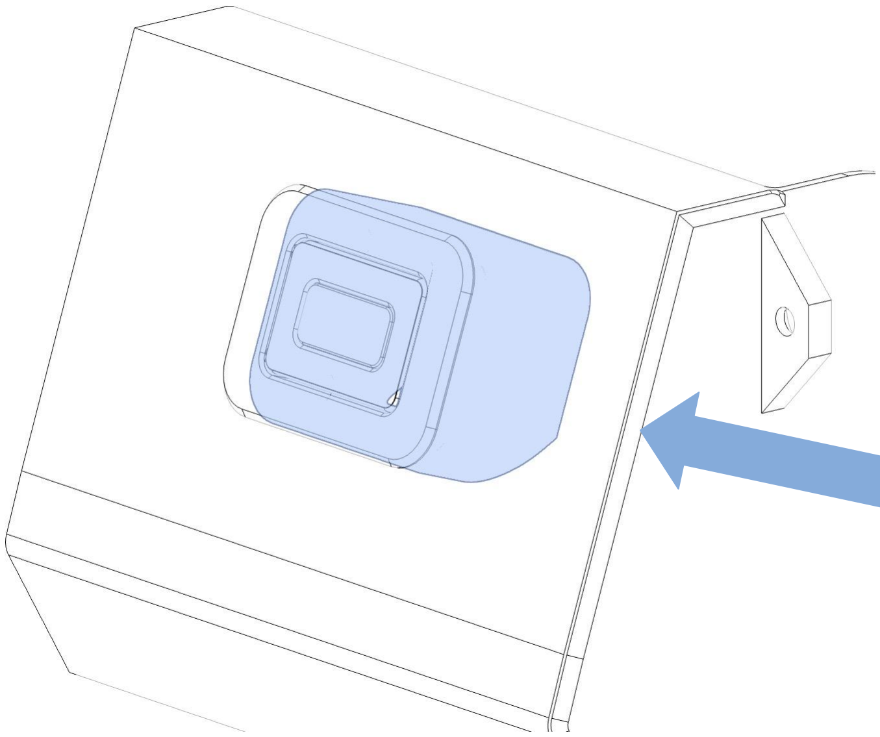
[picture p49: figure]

Place the rear of assembly in the base and squeeze the parts so they fully seat against each other.

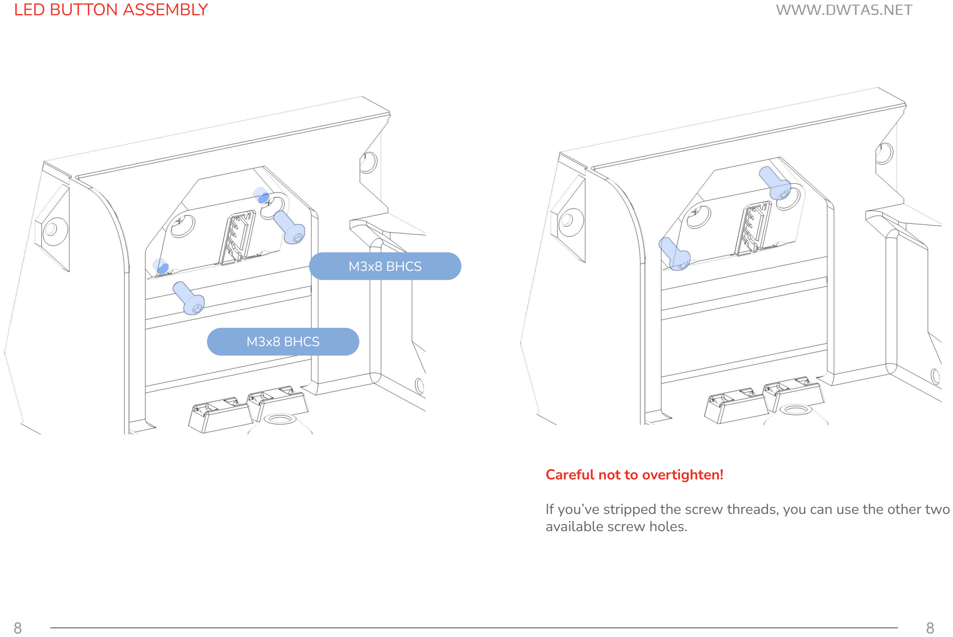
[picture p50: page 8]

LED BUTTON ASSEMBLY | WWW.DWTAS.NET

Careful not to overtighten!

If you’ve stripped the screw threads, you can use the other two available screw holes.

M3x8 BHCS

M3x8 BHCS

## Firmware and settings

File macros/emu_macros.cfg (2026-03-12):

# === EMU Lane Temperature and Humidity Sensors ===

[temperature_sensor Lane_0]
sensor_type: BME280
i2c_address: 118
i2c_mcu: mmu0
i2c_software_scl_pin: mmu0:PB3
i2c_software_sda_pin: mmu0:PB4

[temperature_sensor Lane_1]
sensor_type: BME280
i2c_address: 118
i2c_mcu: mmu1
i2c_software_scl_pin: mmu1:PB3
i2c_software_sda_pin: mmu1:PB4

[temperature_sensor Lane_2]
sensor_type: BME280
i2c_address: 118
i2c_mcu: mmu2
i2c_software_scl_pin: mmu2:PB3
i2c_software_sda_pin: mmu2:PB4

[temperature_sensor Lane_3]
sensor_type: BME280
i2c_address: 118
i2c_mcu: mmu3
i2c_software_scl_pin: mmu3:PB3
i2c_software_sda_pin: mmu3:PB4

[temperature_sensor Lane_4]
sensor_type: BME280
i2c_address: 118
i2c_mcu: mmu4
i2c_software_scl_pin: mmu4:PB3
i2c_software_sda_pin: mmu4:PB4

[temperature_sensor Lane_5]
sensor_type: BME280
i2c_address: 118
i2c_mcu: mmu5
i2c_software_scl_pin: mmu5:PB3
i2c_software_sda_pin: mmu5:PB4

[temperature_sensor Lane_6]
sensor_type: BME280
i2c_address: 118
i2c_mcu: mmu6
i2c_software_scl_pin: mmu6:PB3
i2c_software_sda_pin: mmu6:PB4

[temperature_sensor Lane_7]
sensor_type: BME280
i2c_address: 118
i2c_mcu: mmu7
i2c_software_scl_pin: mmu7:PB3
i2c_software_sda_pin: mmu7:PB4


# === MMU Fan Auto-Control Configuration ===

# === Temperature sensors ===
[temperature_sensor _Lane_0_onboard]
sensor_type: temperature_mcu
sensor_mcu: mmu0
min_temp: 0
max_temp: 130

[temperature_sensor _Lane_1_onboard]
sensor_type: temperature_mcu
sensor_mcu: mmu1
min_temp: 0
max_temp: 130

[temperature_sensor _Lane_2_onboard]
sensor_type: temperature_mcu
sensor_mcu: mmu2
min_temp: 0
max_temp: 130

[temperature_sensor _Lane_3_onboard]
sensor_type: temperature_mcu
sensor_mcu: mmu3
min_temp: 0
max_temp: 130

[temperature_sensor _Lane_4_onboard]
sensor_type: temperature_mcu
sensor_mcu: mmu4
min_temp: 0
max_temp: 130

[temperature_sensor _Lane_5_onboard]
sensor_type: temperature_mcu
sensor_mcu: mmu5
min_temp: 0
max_temp: 130

[temperature_sensor _Lane_6_onboard]
sensor_type: temperature_mcu
sensor_mcu: mmu6
min_temp: 0
max_temp: 130

[temperature_sensor _Lane_7_onboard]
sensor_type: temperature_mcu
sensor_mcu: mmu7
min_temp: 0
max_temp: 130

# === Fans ===

[fan_generic _emu_fan_0]
pin: mmu0:MMU_FAN
max_power: 1
kick_start_time: 0.5

[fan_generic _emu_fan_1]
pin: mmu1:MMU_FAN
max_power: 1
kick_start_time: 0.5

[fan_generic _emu_fan_2]
pin: mmu2:MMU_FAN
max_power: 1
kick_start_time: 0.5

[fan_generic _emu_fan_3]
pin: mmu3:MMU_FAN
max_power: 1
kick_start_time: 0.5

[fan_generic _emu_fan_4]
pin: mmu4:MMU_FAN
max_power: 1
kick_start_time: 0.5

[fan_generic _emu_fan_5]
pin: mmu5:MMU_FAN
max_power: 1
kick_start_time: 0.5

[fan_generic _emu_fan_6]
pin: mmu6:MMU_FAN
max_power: 1
kick_start_time: 0.5

[fan_generic _emu_fan_7]
pin: mmu7:MMU_FAN
max_power: 1
kick_start_time: 0.5


# === MMU Fan Auto-Control (multi-sensor / multi-fan) ===
#
# Pairs each temperature sensor with a fan by index and controls
# that fan with hysteresis based on the paired sensor.
#
# Example:
#   variable_sensors: "Lane_0_onboard,Lane_0_onboard"
#   variable_fans:    "mmu_fan_0,mmu_fan_1"
#
# Notes:
# - Lists must be comma-separated names (no spaces, or strip spaces).
# - If list lengths differ, the shorter length is used (index pairing).
# - FORCE (below) is global: affects all listed fans.

[gcode_macro MMU_FAN_CFG]
description: Holds configuration/state for multi fan controller.
variable_on_temp: 39.0
variable_off_temp: 37.0
variable_poll_s: 5.0
variable_enabled: True
variable_forced: -1                 # -1=AUTO, 0=all OFF, 1=all ON (global)
variable_sensors: "_Lane_0_onboard,_Lane_1_onboard,_Lane_2_onboard,_Lane_3_onboard,_Lane_4_onboard,_Lane_5_onboard,_Lane_6_onboard,_Lane_7_onboard"   # Comma-separated temperature_sensor names
variable_fans:    "_emu_fan_0,_emu_fan_1,_emu_fan_2,_emu_fan_3,_emu_fan_4,_emu_fan_5,_emu_fan_6,_emu_fan_7"  # Comma-separated fan_generic names
variable_warned_len_mismatch: False # internal: warn once per enable
gcode:

[gcode_macro MMU_FAN_MONITOR_ENABLE]
description: Enable automatic multi-fan control.
gcode:
  SET_GCODE_VARIABLE MACRO=MMU_FAN_CFG VARIABLE=enabled VALUE=True
  UPDATE_DELAYED_GCODE ID=_MMU_FAN_LOOP DURATION=0.1
  RESPOND TYPE=echo MSG="MMU multi-fan monitor ENABLED"

[gcode_macro MMU_FAN_MONITOR_DISABLE]
description: Disable automatic control and switch all fans OFF.
gcode:
  SET_GCODE_VARIABLE MACRO=MMU_FAN_CFG VARIABLE=enabled VALUE=False
  UPDATE_DELAYED_GCODE ID=_MMU_FAN_LOOP DURATION=0
  {% set cfg = printer["gcode_macro MMU_FAN_CFG"] %}
  {% set fans = (cfg.fans|string).replace(' ','').split(',') %}
  {% for f in fans %}
    {% if f|length > 0 %}
      SET_FAN_SPEED FAN={f} SPEED=0.0
    {% endif %}
  {% endfor %}
  RESPOND TYPE=echo MSG="MMU multi-fan monitor DISABLED and all fans OFF"

[gcode_macro MMU_FAN_FORCE]
description: Global manual override for all configured fans.
# Usage:
#   MMU_FAN_FORCE S=1   -> Force ALL ON
#   MMU_FAN_FORCE S=0   -> Force ALL OFF
#   MMU_FAN_FORCE S=-1  -> Return to AUTO (per-sensor hysteresis)
gcode:
  {% set s = params.S|default(-1)|int %}
  {% if s not in [-1,0,1] %}
    RESPOND TYPE=error MSG="MMU_FAN_FORCE: S must be -1, 0, or 1"
  {% else %}
    SET_GCODE_VARIABLE MACRO=MMU_FAN_CFG VARIABLE=forced VALUE={s}
    {% set cfg = printer["gcode_macro MMU_FAN_CFG"] %}
    {% set fans = (cfg.fans|string).replace(' ','').split(',') %}
    {% if s == 1 %}
      {% for f in fans %}
        {% if f|length > 0 %}
          SET_FAN_SPEED FAN={f} SPEED=1.0
        {% endif %}
      {% endfor %}
      RESPOND TYPE=echo MSG="MMU fans FORCED ON"
    {% elif s == 0 %}
      {% for f in fans %}
        {% if f|length > 0 %}
          SET_FAN_SPEED FAN={f} SPEED=0.0
        {% endif %}
      {% endfor %}
      RESPOND TYPE=echo MSG="MMU fans FORCED OFF"
    {% else %}
      RESPOND TYPE=echo MSG="MMU fans returned to AUTO mode"
    {% endif %}
  {% endif %}

[delayed_gcode _MMU_FAN_LOOP]
initial_duration: 1
gcode:
  {% set cfg = printer["gcode_macro MMU_FAN_CFG"] %}
  {% if cfg.enabled %}
    {% set forced  = cfg.forced|int %}
    {% set on_t    = cfg.on_temp|float %}
    {% set off_t   = cfg.off_temp|float %}
    {% set sensors = (cfg.sensors|string).replace(' ','').split(',') %}
    {% set fans    = (cfg.fans|string).replace(' ','').split(',') %}
    {% set n_s     = sensors|length %}
    {% set n_f     = fans|length %}
    {% set n_min   = (n_s if n_s < n_f else n_f)|int %}

    {% if n_s != n_f and (not (cfg.warned_len_mismatch|default(False))) %}
      RESPOND TYPE=echo MSG={"MMU_FAN: sensor/fan list length mismatch"}
      SET_GCODE_VARIABLE MACRO=MMU_FAN_CFG VARIABLE=warned_len_mismatch VALUE=True
    {% endif %}

    {% if forced == 1 %}
      {% for i in range(0, n_min) %}
        {% set f = fans[i] %}
        {% if f|length > 0 %}
          SET_FAN_SPEED FAN={f} SPEED=1.0
        {% endif %}
      {% endfor %}
    {% elif forced == 0 %}
      {% for i in range(0, n_min) %}
        {% set f = fans[i] %}
        {% if f|length > 0 %}
          SET_FAN_SPEED FAN={f} SPEED=0.0
        {% endif %}
      {% endfor %}
    {% else %}
      {% for i in range(0, n_min) %}
        {% set s_name = sensors[i] %}
        {% set f = fans[i] %}
        {% if s_name|length > 0 and f|length > 0 %}
          {% set t = printer["temperature_sensor " ~ s_name].temperature|float %}
          {% set cur_speed = (printer["fan_generic " ~ f].speed|default(0.0))|float %}
          {% set cur_state = 1 if cur_speed >= 0.5 else 0 %}
          {% if cur_state == 0 %}
            {% set target_state = 1 if t >= on_t else 0 %}
          {% else %}
            {% set target_state = 1 if t > off_t else 0 %}
          {% endif %}
          {% if target_state != cur_state %}
            {% if target_state == 1 %}
              SET_FAN_SPEED FAN={f} SPEED=1.0
            {% else %}
              SET_FAN_SPEED FAN={f} SPEED=0.0
            {% endif %}
          {% endif %}
        {% endif %}
      {% endfor %}
    {% endif %}

    UPDATE_DELAYED_GCODE ID=_MMU_FAN_LOOP DURATION={cfg.poll_s}
  {% endif %}

# Happy Hare LED additions

[mmu_led_effect mmu_static_white_dim]
define_on:    gates
layers:       static 0 0 top (0.6,0.6,0.6, 0.6)

[mmu_led_effect mmu_ready_white]
define_on:    gates
layers:       breathing 2 0 subtract (0.5,0.5,0.5,0.5)
              static 0 0 top (0.6,0.6,0.6,0.6)

[mmu_led_effect mmu_ready_red]
define_on:    gates
layers:       breathing 2 0 subtract (0.5,0.0,0.0)
              static 0 0 top (0.6,0.0,0.0)

[mmu_led_effect mmu_clockwise_slow]
define_on:    gates
layers:       chase  .5 .5 top    (1,1,1,1), (0.4,0.4,0.4,0.4)

[mmu_led_effect mmu_clockwise_fast]
define_on:    gates
layers:       chase  1  .5 top    (1,1,1,1), (0.4,0.4,0.4,0.4)

[mmu_led_effect mmu_anticlock_slow]
define_on:    gates
layers:       chase  -.5 .5 top   (1,1,1,1), (0.4,0.4,0.4,0.4)

[mmu_led_effect mmu_anticlock_fast]
define_on:    gates
layers:       chase  -1  .5 top   (1,1,1,1), (0.4,0.4,0.4,0.4)
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

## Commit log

2026-02-25 Addet Crimpable jst to Usermods (#24)
    * Addet crimpable jst to user mods
    * changes of text
    * chenges auf pics
    * modified
    * modified: User_Mods/EMU Cable Entry_Crimpable_JST/README.md
    * Update README.md
    * Fix image paths in EMU Cable Entry README
    Updated image paths in README for clarity.
    * Fix formatting for images in README.md
    * Fix image paths and add links in README.md
    Updated image paths to use forward slashes and added additional links.
    * Fix image paths in README.md
    * Modify image display size in README
    Updated README.md to adjust image display size.
    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
    [[a]_Cable_Entry-Inside_crimpable_JST.stl, [a]_Cable_Entry-Outside_crimpable_JST.stl]
2026-02-25 Uploaded CAD model for crimpable JST user mod
    [Cable entry crimpable jst.step]
2026-02-27 Updated blobifier filament change g-code.
2026-02-28 Moved combiners no sensor to main folder. Renamed folder so encoder is not referenced as its a deprecated option
    [12_Tooth_Encoder_Slotted_Wheel.stl, 688_Bushing.stl, Combiner_1-1.stl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]
2026-02-28 Moved sensored combiner, encoders to deprecated options folder
    [12_Tooth_Encoder_Slotted_Wheel.stl, 688_Bushing.stl, Encoder_Left.stl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]
2026-03-02 Update print settings for idler roller axle and stepper tension arm.
2026-03-03 DFRobot SHT31 holder
    [DFRobot_SHT31_Holder.f3d, DFRobot_SHT31_Holder.step, DFRobot_SHT31_Holder.stl]
2026-03-03 DFRobot SHT31 holder (#25)
    [DFRobot_SHT31_Holder.f3d, DFRobot_SHT31_Holder.step, DFRobot_SHT31_Holder.stl]
2026-03-09 mods-to-main added to readme
    [Rim_roller_square_nut_1_hole.step, Rim_roller_square_nut_1_hole.stl]
2026-03-11 Minor refinements to v1.1 of the LED PCB
    [BOM_EMU_Multi_LED_Button_PCB_EMU_Multi_LED_Button_PCB_rev1_1.csv]
2026-03-11 EMU LED Button PCB manual upload
2026-03-11 updated hatch board vendors to include JB3D
2026-03-11 Updated recommended upgrades with Eject button multi-LED PCB
2026-03-12 Updated emu_macros.cfg with latest LED effects for LED Button PCB
    [emu_macros.cfg]
2026-03-12 Bump BME280.py to latest klipper version
2026-03-12 Flipped button rear STL file & CAD for 4 LED PCB board. Update manual.
    [Button_Rear.stl]
2026-03-15 updated main page readme to refine filamentalist use wording.
2026-03-16 Uploaded beta filamentalist frame with polyhole bearings
    Aiming to fix rear bearing occasional cracking issue if tolerances are not adequately calibrated
    [Chassis_L_688_Bearing[polyhole].stl, Chassis_R_688_Bearing[polyhole].stl, Filamentalist_frame_polyhole_bearings.step]
2026-03-16 Polyhole testing - octagonal model and tolerance options
    [Chassis_L_688_Bearing_12_faces_0.05_inset.stl, Chassis_L_688_Bearing_8_faces_0.05_inset.stl, Chassis_L_688_Bearing_8_faces_0.1_inset.stl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]
2026-03-17 LED PCB readme initial commit
2026-03-17 Updated LED PCB readme page with video and links.
2026-03-17 Updated hatch board with updated pick and place files to match available parts on JLCPCB
    [BOM_PCB1_PCB1_2026-01-19.csv, BOM_PCB1_PCB1_2026-03-17.csv, PickAndPlace_PCB1_2026-03-17.csv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]
2026-03-18 Rubber Installer (#42)
    User Mod rubber installer
    [EMU Tube Cutter - 30mm.stl, Rubber tube installer.stl]
2026-03-19 Removed Beta filamentalist frame, while fixing issue with frame alignment.
    [Filamentalist_frame_polyhole_bearings.step]

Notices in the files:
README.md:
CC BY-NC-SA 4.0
